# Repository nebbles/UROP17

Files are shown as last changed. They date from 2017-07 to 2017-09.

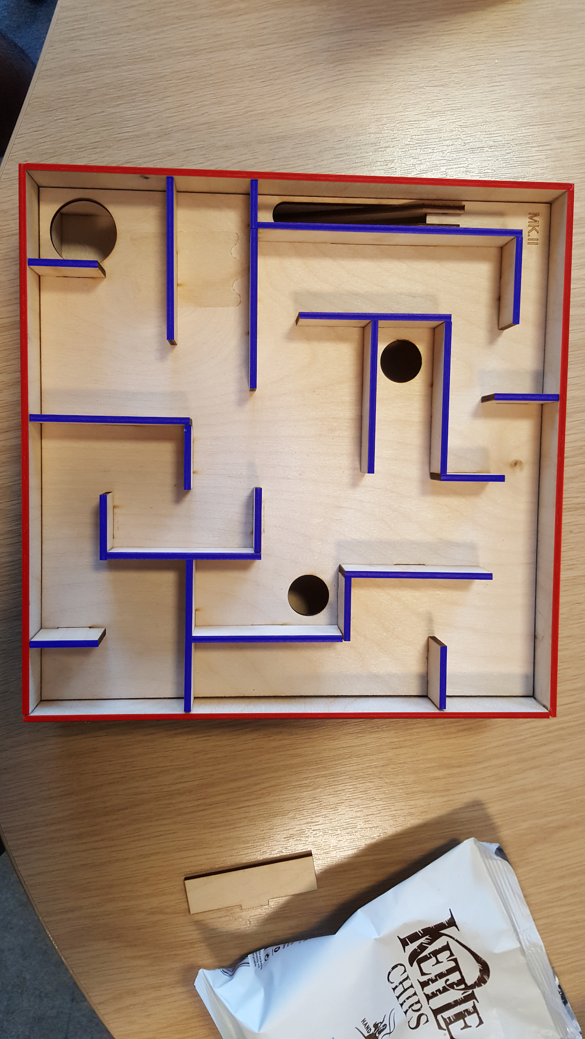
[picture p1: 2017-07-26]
Exercises/epxthreshdetect/build/maze5-rb.png

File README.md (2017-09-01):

# UROP17
Undergraduate Research Opportunity Programme Project Summer 2017  
_Exploration into Machine Learning with the Nvidia Jetson Tegra X2 Developer Kit_  

> Shreyus Bagga  
> Benedict Greenberg  

### [Weekly notes](/Weekly-Notes.md)

### Milestones

`2017-Aug-27` Host computer controlling motors' speed via Arduino.  
`2017-Aug-25` Successfully communicate from TX2 to Arduino.  
`2017-Aug-03` Successfully controlling motors with Arduino.  
`2017-Jul-19` Filtering of image through RGB thresholding to detect walls of maze.  
`2017-Jul-17` On-board TX2 camera utilised in a simple object-tracking program (OpenCV 3.3-rc).  
`2017-Jul-07` Project defined: ML maze balancing puzzle.  
`2017-Jul-05` Nvidia Tegra X2 successfully setup and running SSH, live camera feeds, and video analysis.

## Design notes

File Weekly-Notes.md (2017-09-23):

# Weekly Note Log of Progress

## Contents

- [x] [Week 1](#week-1)
- [x] [Week 2](#week-2)
- [x] [Week 3](#week-3)
- [x] [Week 4 & 5](#week-4--5)
- [x] [Week 6](#week-6)
- [x] [Week 7](#week-7)
- [x] [Week 8 & onwards...](#week-8--onwards)

# Week ```1```
[_Back to top_](#contents)

1. [Set-up of Nvidia Tegra X2](#set-up-of-nvidia-tegra-x2)
2. [Workflow](#workflow)
3. [Idea Generation](#idea-generation)

## Set-up of Nvidia Tegra X2

Commence setting up process. This involved sourcing a display, connection with HDMI cable. TX2 was flashed using the set-up process described in a [video](https://www.youtube.com/watch?v=D7lkth34rgM) by another developer.

When installing the [Nvidia JetPack 3.0 package](https://developer.nvidia.com/embedded/jetpack) the post-flash installation procedure was started manually after connecting the TX2 to the internet via WiFi. This was important due to connection restrictions at Imperial. Post-installation the TX2 was ready for use with preinstalled packages providing a number of ML examples.

## Workflow

### Host computers

Workflow initially established included using CyberDuck for the SFTP protocol to directly edit and transfer files to the TX2. In parallel, FileZilla was used on linux. Ubuntu and MacOS were both used to write initial example code and send to the TX2.

### Compiling

Compilation was decidedly done for all programs thus far on the target machine due to cross-compilation errors when compiling on host due to different hardware.

On-target-compilation of __test.cpp__ was at first successfully executed (to __Test__) using:
```bash
g++ test.cpp -o Test `pkg-config opencv --cflags --libs`
# Followed by executing the output file
./Test
```
However this was not the recommended approach due to usage of OpenCV usually requiring `cmake` and a `CMakeList.txt`. As such with further investigation on why this approach wouldn't work using Nvidia's [official guide](https://www.youtube.com/watch?v=gvmP0WRVUxI), a fic was found to ensure the CMake would properly compile. This was with:
```bash
cmake -D CUDA_USE_STATIC_CUDA_RUNTIME=OFF
```
## Idea Generation

A number of initial ideas on the application on computer vision and machine learning were discussed and analysed in the first week for potential projects.

 - __Concept: Indoor Guidance for the visually impaired__ - this concept would deliver an example into the possible future of indoor mapping and guidance systems for the visually impaired. The system would rely on a image mapping system and machine learning to allow the guidance system to locate itself accurately in an indoor environment and provide useful informaiton to the user about getting to their target location.
 - __Concept: Dynamic control of a lightweight drone in busy areas__ - this concept aims to provide intelligent control of a drone populated by unpredicatble moving items (such as a person walking through the flying zone) and to intelligently control the drone so as to avoid these disruptions and still maintain flight to pre-determined goal.
 - __Concept: Control and mastery of a balancing puzzle maze__ - this concept aims to provide a control unit with two axis tilt output on a ball bearing maze. The control unit would use a camera input to analyse the puzzle just as a human would and work out a number of dynamic puzzle simultaneously such as balancing the ball bearing, finding optimal routes through a maze, and avoiding failure conditions (such as holes in the maze).

Additional modifications on these concepts included a possible RC vehicle that had to navigate through unknown terrain using ML techniques to improve driving.

# Week ```2```
[_Back to top_](#contents)

## Project Planning

Project planning is a key part in achieving any long term academic goal. As such, an approximate initial Gantt chart was created to start informing deadlines for various aspects of the projects, and to start identifying dependencies.

## Hardware Design

Hardware design began with modelling the tilt mechanism and maze in 3D modelling software SolidWorks & Fusion 360. This would inform the manufacturing of the hardware set-up and is a necessary step in the usage of workshops. Workshop build will begin next week with ordering of hardware electronics and machining of the maze. Renders and engineering drawings will be added to the repository upon completion.

## Image Recognition

Initial work into image feature recognition involved using OpenCV 3 and the new tracking API to identify different shapes of different colours in precaptured video footage.

GStreamer 1.0 was configured with OpenCV 3.3-rc to allow access to the on-board camera through C++ programs making use of the OpenCV library. The following line was required to access the camera feed:
`nvcamerasrc ! video/x-raw(memory:NVMM), width=(int)1920, height=(int)1080,format=(string)I420, framerate=(fraction)60/1 ! nvvidconv flip-method=2 ! video/x-raw, format=(string)BGRx ! videoconvert ! video/x-raw, format=(string)BGR ! appsink`

# Week ```3```
[_Back to top_](#contents)

## First Object-Tracking Program

The first effective object-tracking program made use of the Tracking API in the OpenCV 3 extra modules. More precisely, through `"opencv2/tracking.hpp"`. At the start of the program, the user chooses whether to use a video or the on-board camera. The user then draws a rectangle around the object that they wish to track, on the first frame of video input.

The next task is to have a pre-determined image for the machine to recognise and detect at the start, without a user's input.

# Week ```4``` & ```5```
[_Back to top_](#contents)

Over the two week period:
- First iterations of the maze were produced.
- First design of mechanism was assembled.
- Initial work into Arduino motor control was established.

Work to follow up with:
- Complete Arduino control of two stepper motors.
- Redesign of maze and mechanism to eliminate problems.
- Assembly of maze with motors.
- Establish Serial connection between Tegra program and Arduino (with custom written library).

# Week ```6```
[_Back to top_](#contents)

## Maze Redesign

The maze mechanism and build had to be redesigned and manufactured to implement new changes and improve on the previous two versions.

Mk.III has a design which streamlines the tilting mechanism as much as possible, whilst preparing for the inevitable addition of the stepper motors and timing belts.

Final addition and repairs still to be made include the upgraded ramp (v2) and fixed MAZE_BOARD. These fixes can all be found under v2 prefix of the model files.

## Arduino & Motors

Motor 1 using GPIO 3-6, connected to IN1-4 MOTOR A.  
Power supply set at 4.8 V with maximum 0.5 A.  
Motor 2 using GPIO 8-11, connected to IN1-4 MOTOR B.  

Support for communicating to the Arduino from the TX2 has been implemented. In order fo the USB drivers to work properly on the Tegra, a new kernal had to be installed. This allowed for communication over port ```/dev/ttyACM1```. In additon to this, a [quick program](/coms/arduino_com_v2.cpp) has been written to send simple commands over Serial. This will be deveoped into a library that the machine learner or algorithm can do to balance and control the maze.

The Arduino runs [the slave](/coms/TX2Read_v3/) to the controller program. This has integrated motor control referencing earlier work done with [**stepper_new**](/arduino/stepper_new), a custom test Arduino program. In uses a number of custom built functions such as ```getSerial()``` to understand what the controller is commanding. This as of the end of the week was working until the ```switch(command.motor)``` was implemented. As a result a number of ```// TODO``` comments have been made to improve this program.

# Week ```7```
[_Back to top_](#contents)

Week began with fixing bugs in the Arduino program. These issues will be expanded on...  
The controller program running on the Tegra was adjusted for minor fixes to work with the latest version of `TX2Read.ino`.

A [belt and pulley](https://www.amazon.co.uk/MyArmor-Timing-Pulley-2GT-6mm-Opening/dp/B018DZ28V2/) was utilised to connect the two tilting planes to connect to two 4mm aluminium rods in the lower section of the maze assembly. A gear transmission was selected for conversion from the stepper motor to the rods. As a result of neglecting the design in earlier iterations, the outer casing had to be redesigned to accomodate the stepper motors and two rods. In addition there were a number of fixes to earlier designs of the Mk.III maze design.

Transmission was designed on [Gear Generator](http://geargenerator.com/#200,200,100,6,1,0,13521.300000005276,2,1,8,2,4,27,-90,0,0,16,4,4,27,-60,0,0,2,154) where the designs were saved as an SVG. These were converted to DXF with [CloudConvert](https://cloudconvert.com/svg-to-dxf) for the sake of CAD modelling in SolidWorks. These designs were then further modified to be compaitble with the 4mm rods and the [28BYJ-48 Stepper Motors](http://www.instructables.com/id/BYJ48-Stepper-Motor/).

The following files were used in the CAD modelling of the maze casing for reference:
- [Stepper motor (GrabCAD)](https://grabcad.com/library/28byj-48-5v-stepper-motor-1)
- [Stepper driver (GrabCAD)](https://grabcad.com/library/uln2003-unipolar-stepper-driver-board-1)
- [Arduino Uno (GrabCAD)](https://grabcad.com/library/arduino-uno-r3-1)

Version 4 of the Mark III hardware designs were created to implement these new additions. Mostly all were further laser cut pieces to replace or add to the existing hardware, however the gears were custom modelled and 3D printed for purpose. The files for these can be found in the Mark III CAD folder.

# Week ```8``` & onwards...
[_Back to top_](#contents)

Mark III V6 marked the final version of the iterative design. It fixed a number of issues with the hardware which prevented the the two axis tilt from working along one axis. This resulted in a redesign to ensure the pulleys were positioned centrally in line with the pivots on each of the maze supporting sections.

A brief look into the interface of the built-in camera module on the TX2 revealed that they use an expensive propretory connector made by Samtec. Related searches to this camera module and I/O port include:
- Samtec HQCD
- Samtec Q strip
- Samtec [interface catalogue](http://suddendocs.samtec.com/catalog_english/eqcd.pdf)
- Samtec [EQCD](https://www.samtec.com/products/eqcd#related)

Small alterations were brought to TX2Read which brought it forward to version 4. This included an updated command library so that quick control to bring both stepper motors to a halt and to deselect any active motors available. This was used, as before, in tandem with the [AccelStepper library](http://www.airspayce.com/mikem/arduino/AccelStepper/classAccelStepper.html#a5dce13ab2a1b02b8f443318886bf6fc5) which provides enhanced stepper control over the standard stepper library.

Xcode was used to begin writing the main TX2 program. `ai-maze` was created and initially included the adapted `TX2Write` program developed for testing the maze control with motors. It then was updated to include PID control within the command setting procedure so as to take the current position of the ball and move it toward a target coordinate.

For the complete program, it became apparent that multiple threads (or processes) would be needed to manage the multiple resources and updating required by different components of the maze controller. The functions were split into three threads running from the main thread.

- **Tracking**  
This thread manages the rapid updating of the current position of the ball using OpenCV and its tracking features. This thread needs to manage this resource separately as it needs to be highly accurate and updated regularly.

- **Navigation**  
This thread manages the updating of the target coordinate used by the Balance thread and also uses the current ball position resource provided by the tracking thread. It uses this and its end goal to determine a route through the maze. The maze is recognised and analysed using the birds eye camera feed of the maze and then selects the next required target for the Balance thread.

- **Balance (Control & Command)**  
This consists of taking the current position of the ball and using PID to determine what the motor commands should be to get the ball to its target position. It also sends these commands over USB Serial to the Arduino which interprets and changes the motors.

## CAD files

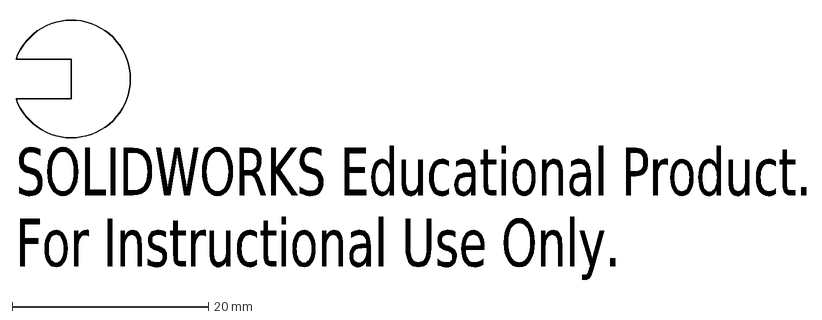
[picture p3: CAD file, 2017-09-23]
Manufacture/Lasercutting/40-TRIAL.DXF
SOLIDWORKS Educational Product.
For Instructional Use Only.

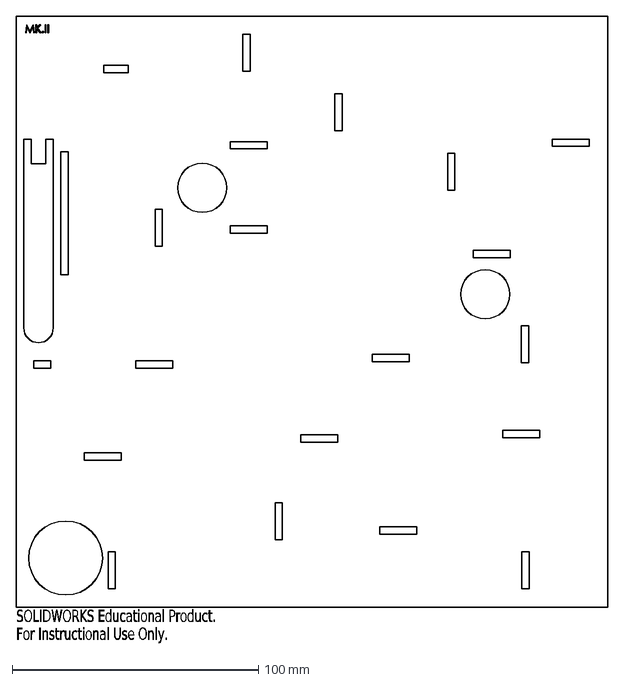
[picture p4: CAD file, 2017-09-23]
Manufacture/Lasercutting/PLY-3MM/Maze_mk2_Board.DXF
SOLIDWORKS Educational Product.
For Instructional Use Only.

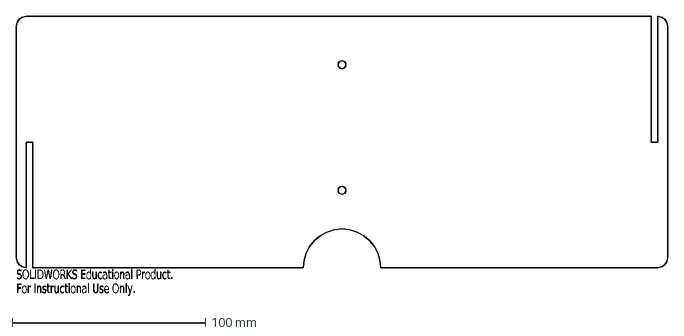
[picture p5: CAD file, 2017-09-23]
Manufacture/Lasercutting/PLY-FIB-3400um/MKI/Casing_wall_mk1.DXF
SOLIDWORKS Educational Product.
For Instructional Use Only.

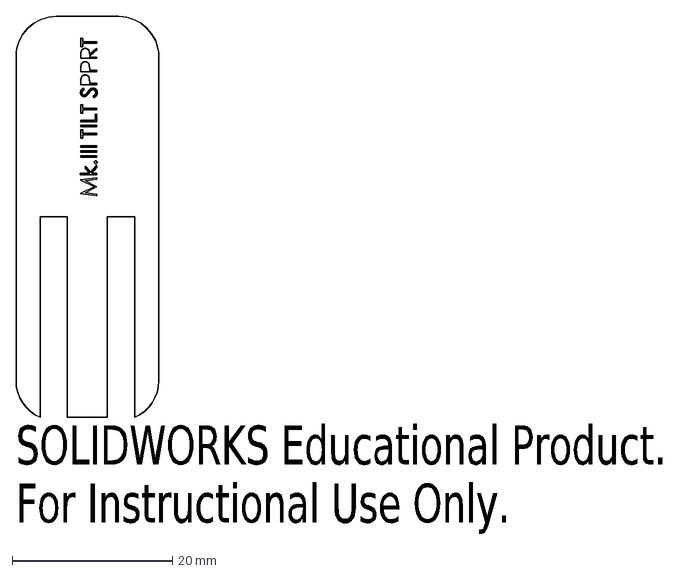
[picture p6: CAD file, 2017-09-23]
Manufacture/Lasercutting/PLY-FIB-3400um/MKIII_DXF/MK3_TILT_SUPPORT.DXF
SOLIDWORKS Educational Product.
For Instructional Use Only.

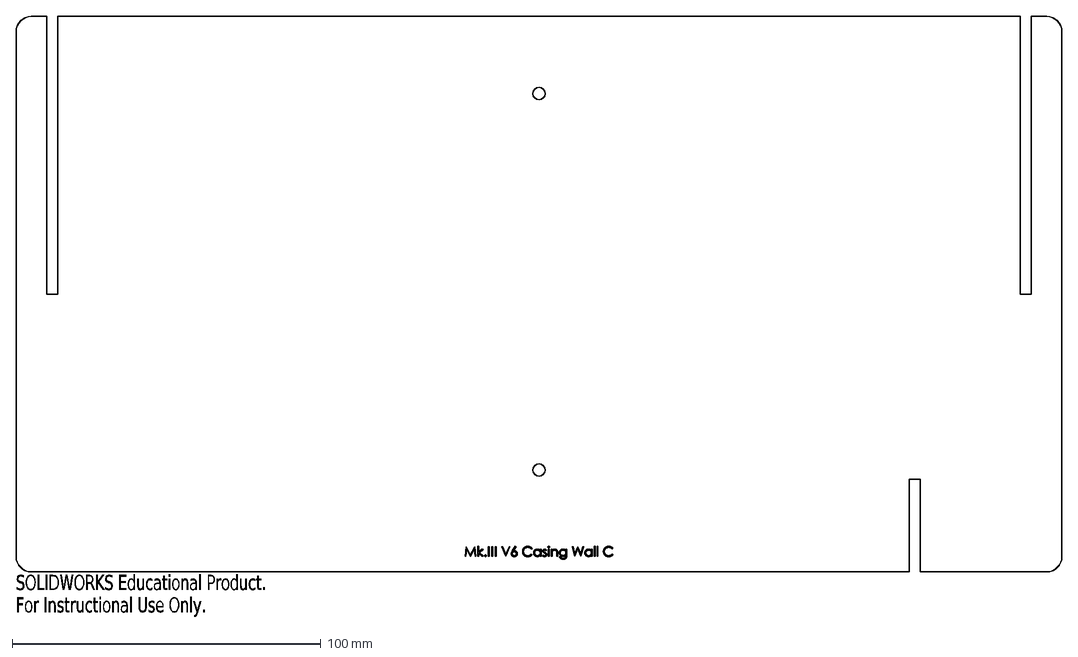
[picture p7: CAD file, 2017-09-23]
Manufacture/Lasercutting/PLY-FIB-3400um/MKIII_V6_DXF/MK3_V6_CASING_WALL_C.DXF
SOLIDWORKS Educational Product.
For Instructional Use Only.

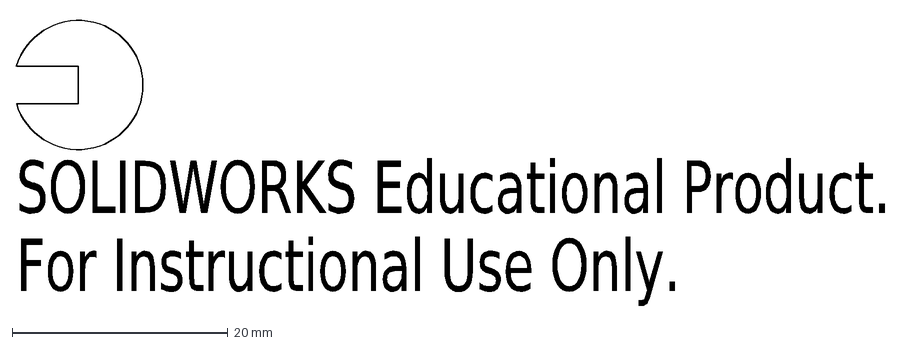
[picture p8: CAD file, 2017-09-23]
Manufacture/Lasercutting/35-TRIAL.DXF
SOLIDWORKS Educational Product.
For Instructional Use Only.

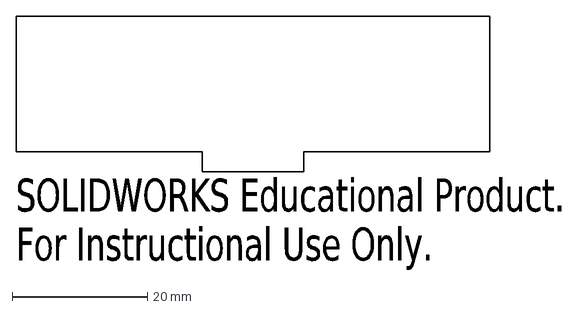
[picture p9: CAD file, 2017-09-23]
Manufacture/Lasercutting/PLY-3MM/Maze_mk2_Wall_70.DXF
SOLIDWORKS Educational Product.
For Instructional Use Only.

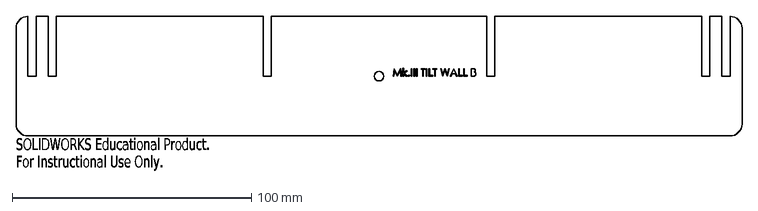
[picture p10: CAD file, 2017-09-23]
Manufacture/Lasercutting/PLY-FIB-3400um/MKIII_DXF/MK3_TILT_WALL_B.DXF
SOLIDWORKS Educational Product.
For Instructional Use Only.

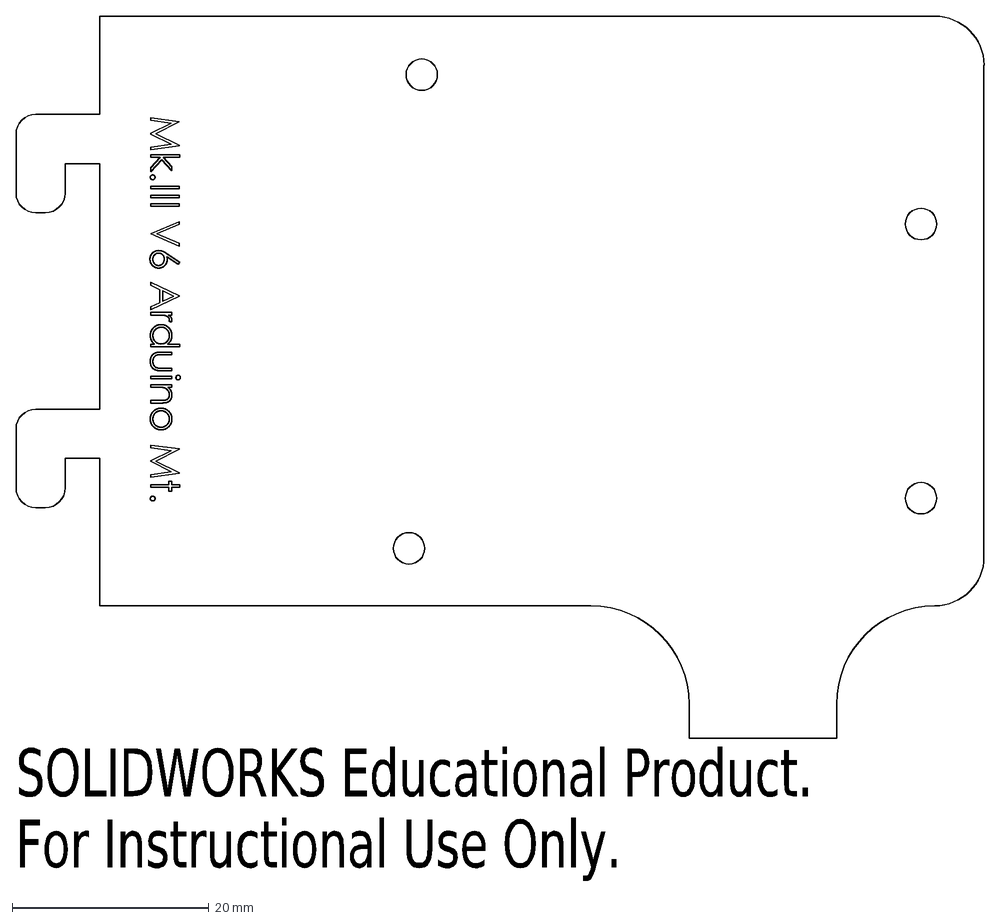
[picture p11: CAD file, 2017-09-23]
Manufacture/Lasercutting/PLY-FIB-3400um/MKIII_V6_DXF/MK3_V6_CASING_MT_ARDUINO.DXF
SOLIDWORKS Educational Product.
For Instructional Use Only.

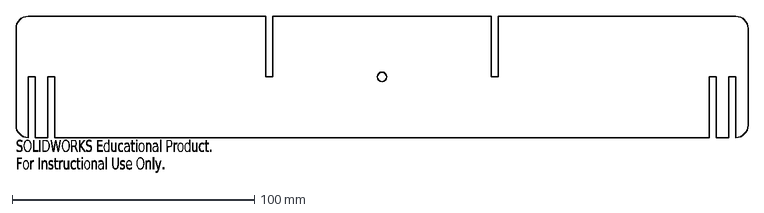
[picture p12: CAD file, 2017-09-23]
Manufacture/Lasercutting/PLY-3MM/TILT_INNER_WALL_A_V1.DXF
SOLIDWORKS Educational Product.
For Instructional Use Only.

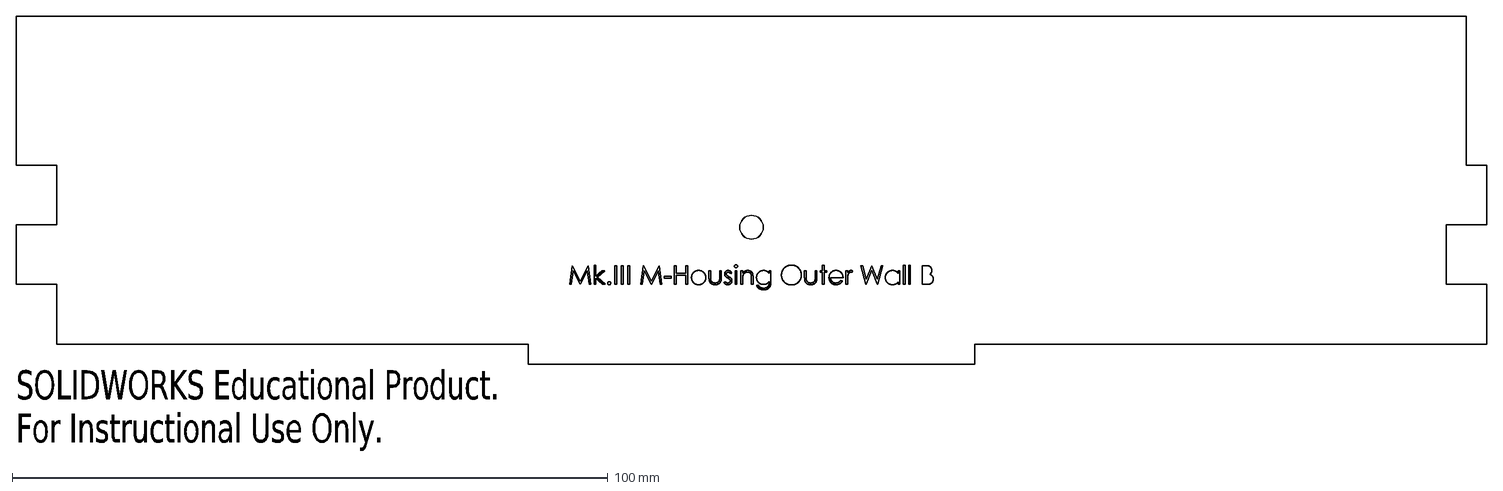
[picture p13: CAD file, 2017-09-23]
Manufacture/Lasercutting/PLY-FIB-3400um/MKIII_DXF/MK3_M-HOUSING_OUTER_B.DXF
SOLIDWORKS Educational Product.
For Instructional Use Only.

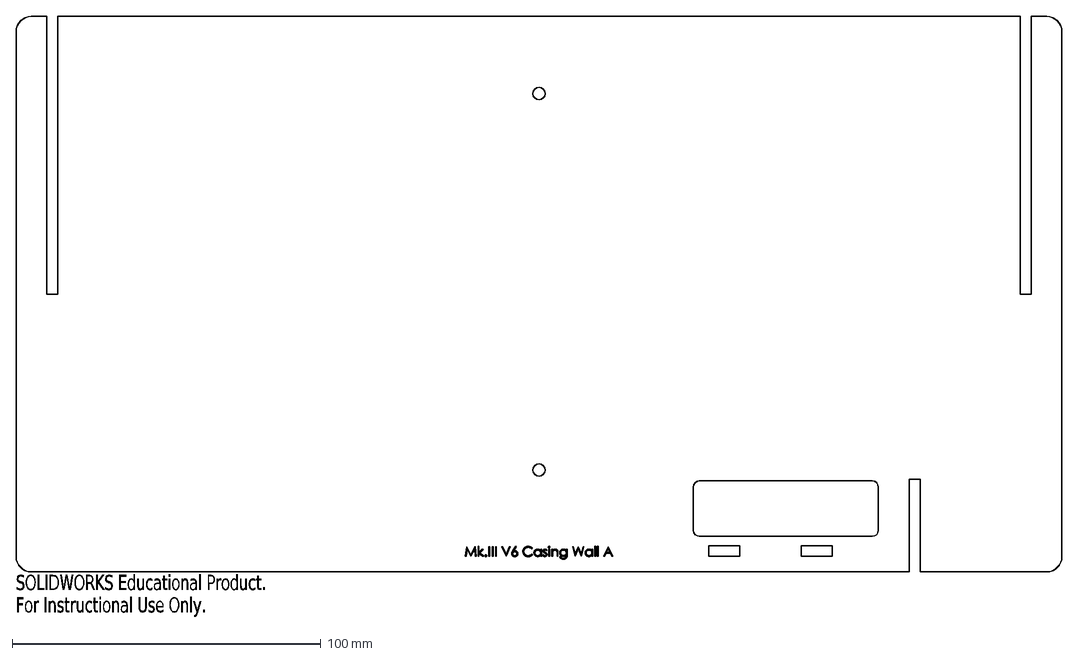
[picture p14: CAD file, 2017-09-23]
Manufacture/Lasercutting/PLY-FIB-3400um/MKIII_V6_DXF/MK3_V6_CASING_WALL_A.DXF
SOLIDWORKS Educational Product.
For Instructional Use Only.

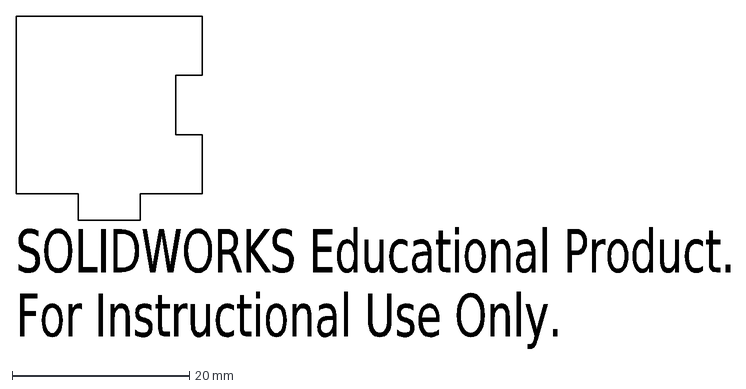
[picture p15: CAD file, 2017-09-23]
Manufacture/Lasercutting/PLY-3MM/Maze_Wall_1.DXF
SOLIDWORKS Educational Product.
For Instructional Use Only.

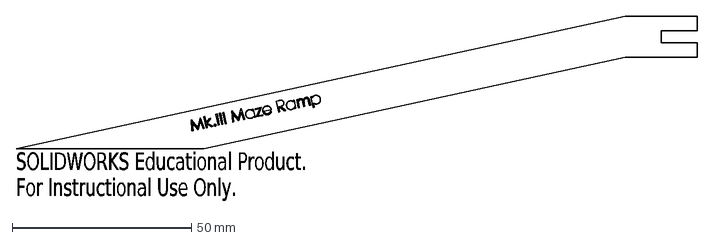
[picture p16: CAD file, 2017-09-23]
Manufacture/Lasercutting/PLY-FIB-3400um/MKIII_DXF/MK3_MAZE_RAMP.DXF
SOLIDWORKS Educational Product.
For Instructional Use Only.

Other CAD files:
Manufacture/Lasercutting/PLY-FIB-3400um/MKIII_V6_DXF/MK3_V6_CASING_WALL_B.DXF
Manufacture/Lasercutting/PLY-3MM/TILT_INNER_WALL_B_V1.DXF
Manufacture/Lasercutting/PLY-FIB-3400um/MKIII_DXF/MK3_CASING_WALL_B.DXF
Manufacture/Lasercutting/PLY-FIB-3400um/MKIII_V6_DXF/MK3_V6_CASING_MT_BOARD_X.DXF
Manufacture/Lasercutting/PLY-3MM/Maze_Base.DXF
Manufacture/Lasercutting/PLY-3MM/Maze_Board.DXF
Manufacture/Lasercutting/PLY-3MM/Maze_Ramps.DXF
Manufacture/Lasercutting/PLY-3MM/Maze_Wall_2.DXF
Manufacture/Lasercutting/PLY-3MM/Maze_Wall_3.DXF
Manufacture/Lasercutting/PLY-3MM/Maze_Wall_Inner.DXF
Manufacture/Lasercutting/PLY-3MM/Maze_Wall_Outer.DXF
Manufacture/Lasercutting/PLY-3MM/Maze_mk2_Wall_30.DXF
Manufacture/Lasercutting/PLY-3MM/TILT_INNER_Support_V1.DXF
Manufacture/Lasercutting/PLY-FIB-3400um/MKIII_DXF/MK3_CASING_WALL_A.DXF
Manufacture/Lasercutting/PLY-FIB-3400um/MKIII_DXF/MK3_M-HOUSING_BASE.DXF
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

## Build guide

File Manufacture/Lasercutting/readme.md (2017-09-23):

Original plywood board from 10 Princes Gardens Hackspace was 3mm thickness cut with 'Birch-3mm' on laser cutter.

New plywood, fibre composite from Skempton Workshops cut best at 'Birch-4mm' with CAD slots at 3.4mm for an interference fit.

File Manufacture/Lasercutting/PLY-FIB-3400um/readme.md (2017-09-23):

# Material

Sourced from IDEAS Lab, Skempton.  
4mm laser-cutter plywood fibre composite.  

# CAD

CAD should use interference slots of 3.4mm  

# Manufacturing - Laser cutting

### IC Advanced Hackspace, 10 Princes Gardens.  
Settings:  
<table>
  <tr>
    <td>Material</td>
    <td><b>Natural > Wood > Medium Wood > Birch</b></td>
  </tr>
  <tr>
    <td>Intensity adjustment</td>
    <td>Engraving @ <b>+20%</b> <br>Cutting @ <b>+50%</b></td>
  </tr>
  <tr>
    <td>Material thickness</td>
    <td><b>4.5 mm</b></td>
  </tr>
</table>

### IDEAS Lab, Skempton
Settings:  
<table>
  <tr>
    <td>Material</td>
    <td><b>Natural > Wood > Medium Wood > Birch</b></td>
  </tr>
  <tr>
    <td>Intensity adjustment</td>
    <td><i>Default settings</i></td>
  </tr>
  <tr>
    <td>Material thickness</td>
    <td><b>4.0 mm</b></td>
  </tr>
</table>

Set-up is just like hackspace. 
Application is called 'UCP' on Windows. 
Use Coreldraw as normal. 
Settings are usually manual using the sheet provided. 
Use custom settings determined through experimentation where necessary for the correct cut. 
Positioning can be done with door open.
Bed size is approx 600x450mm.

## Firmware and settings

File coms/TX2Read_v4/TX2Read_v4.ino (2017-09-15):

// TX2Read
// Program by BG.
// v3: 25 August 2017
// v4: 05 September 2017
//
// Communication received from Nvidia TX2 running TX2Write or newer.
// Controlling 28BYJ-48 Stepper Motor with ULN2003 driver.
//
// v4:
// - set motor (M) to position (P) with call command "M,P."
//      M = -1 selects no motors
//      M = 0 selects both motors
//      M = 1 selects motor A
//      M = 2 selects motor B
//      P can = any Real Integer value
// - call "stop" over serial to shutdown both motors
// - call "a" over serial to shutdown motor A immediately
// - call "b" over serial to shutdown motor B immediately
//

#include <AccelStepper.h> // advanced Stepper lib on Arduino
#define HALFSTEP 8 // required by AccelStepper

// Motor pin definitions
#define motorAPin1  3     // IN1 on the ULN2003 driver 1
#define motorAPin2  4     // IN2 on the ULN2003 driver 1
#define motorAPin3  5     // IN3 on the ULN2003 driver 1
#define motorAPin4  6     // IN4 on the ULN2003 driver 1

#define motorBPin1  8     // IN1 on the ULN2003 driver 2
#define motorBPin2  9     // IN2 on the ULN2003 driver 2
#define motorBPin3  10    // IN3 on the ULN2003 driver 2
#define motorBPin4  11    // IN4 on the ULN2003 driver 2

// Initialize with pin sequence IN1-IN3-IN2-IN4
// for using the AccelStepper with 28BYJ-48
AccelStepper stepper1(HALFSTEP, motorAPin1, motorAPin3, motorAPin2, motorAPin4);
AccelStepper stepper2(HALFSTEP, motorBPin1, motorBPin3, motorBPin2, motorBPin4);

char inChar; // character received over Serial
String inString; // cumulative characters saved as String
int number; // value of converted string

struct command_structure { // stores two elements that make up command
  int motor = 0; // motor being controlled, 0 is for both.
  int mspeed = 0; // speed that motor should set to
};
command_structure command; // construct object of struct
int cm_idx = 0; // command number for strings of commands

struct motor_states_struct { // stores the semi-permanent state of motors
  int Aspeed = 0;
  int Bspeed = 0;
};
motor_states_struct motorstate; // construct object

void stopAll() {
  stepper1.stop();
  stepper1.disableOutputs();
  stepper2.stop();
  stepper2.disableOutputs();
  command.motor = -1; // Set ongoing command to neither motor
}
void stopA() {
  stepper1.stop();
  stepper1.disableOutputs();
  command.motor = -1; // Set ongoing command to neither motor
}
void stopB() {
  stepper2.stop();
  stepper2.disableOutputs();
  command.motor = -1; // Set ongoing command to neither motor
}

void setup() {
  Serial.begin(9600);
  while (!Serial) {
    ; // wait for Serial to establish
  }
  Serial.println("TX2Read v4");
  Serial.println("CHECK MOTORS are correctly connected.");
  Serial.println(" ");
  Serial.println("Motor A: IN1-4 connected to DIGITAL 3-6");
  Serial.println("Motor B: IN1-4 connected to DIGITAL 8-11");
  Serial.println(" ");

  { // Stepper motor setup sequence
    // Establish initial settings for motors

    int maxspeed = 1500;
    int maxaccel = 1500;

    stepper1.setMaxSpeed(maxspeed);
    stepper1.setSpeed(maxspeed);
    stepper1.setAcceleration(maxaccel);

    stepper2.setMaxSpeed(maxspeed);
    stepper2.setSpeed(maxspeed);
    stepper2.setAcceleration(maxaccel);

    stepper1.run();
    stepper2.run();
    stopAll();
  }

}

void loop() {
  if (Serial.available() > 0) {
    getSerial();
    // TODO; add a way to change motor settings
  }
  action();
}

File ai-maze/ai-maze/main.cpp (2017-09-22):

//
// AI-Maze
// Created by Shreyus Bagga and Benedict Greenberg
// September 2017
// Copyright © 2017. All rights reserved.
//
// main.cpp
//
// Version 1.0
// Created: 19 September 2017
// Last modified: 19 September 2017
//
// On Macintosh, compiled program must be run with 'sudo'
// All other instructions are within program. Run from the terminal.
//

#include <iostream>
#include <stdio.h>
#include <sstream>

#include "tx2write.hpp"

using namespace std;

int main()
{
    cout << "main.cpp" << endl;
    
    // set up x and y position variables
    // start up threads
    // wait for user commands
    // close down threads correctly on close
    return 0;
}

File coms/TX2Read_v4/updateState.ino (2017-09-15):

// updateState() takes an existing or new command (stored in struct 'command'
// and updates the state of the motors. This state will be acted on by the
// action() function which calls this function.
//
// This ensures that the motors are not always updated with a new command.
//

void updateState() {
  if ( command.motor < -2 || command.motor > 2 ) {
    Serial.println("command.motor is out of range. Setting as default '0'");
    command.motor = 0;
  }

  // DEBUG
  //  if ( command.motor == -1 ) {
  //    Serial.println("-1 means no motor is selected");
  //  }

  switch (command.motor) {
    case -2:
      stepper1.setAcceleration(command.mspeed);
      stepper2.setAcceleration(command.mspeed);
      Serial.print("Acceleration for both motors changed to: ");
      Serial.println(command.mspeed);
      command.motor = -1; // Set ongoing command to null
      break;

    case -1:
      // This case is null. Nothing is changed/affected.
      break;

    case 0: // both motors are chosen
      motorstate.Aspeed = command.mspeed;
      motorstate.Bspeed = command.mspeed;
      break;

    case 1: // only motor A
      motorstate.Aspeed = command.mspeed;
      break;

    case 2: // only motor B
      motorstate.Bspeed = command.mspeed;
      break;
  }
}

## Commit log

2017-08-23 Upload initial arduino work files
2017-08-24 added arduino TX2Read docs
2017-08-25 added TX2Read_v3
    Noticed weird bug with motors disobeying the stop command since adding
    the switch(command.motor). Have added TODO comments to be finished over
    the weekend.
    [TX2Read_v3.ino, action.ino, getSerial.ino]
2017-08-29 test reading from arduino
    Incomplete test of reading serial from arduino
2017-08-29 new arduino write program
2017-09-15 TX2Read v4 upload
    v4 of TX2Read now uses motor positions instead of motor speeds. It also
    introduces a slightly modified way of command format so that more
    advanced commands can be sent such as changing max speed or
    acceleration.
2017-09-23 Add laser cutting files from projects repo
    [35-TRIAL.DXF, 40-TRIAL.DXF, Casing_wall_mk1.DXF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]
